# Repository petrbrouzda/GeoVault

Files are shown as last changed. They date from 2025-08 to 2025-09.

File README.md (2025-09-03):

# GeoVault - GPS trezor

Kouzelná krabička, která se sama otevře až na správném místě. A informace, jak najít správné místo, nedává moc konkrétně. Uváděné kilometry k cíli udává po skocích, tj. nestačí si zajít na dvě různá místa a zbytek vyřešit triangulací. 

Kilometry ukazuje po následujících blocích:
```
int kilometers[] = { 2, 3, 5, 10, 18, 30, 55, 72, 82, 90, 110, 150, 200, -1 };
```

Pro vzdálenost menší než 2 km ukazuje metry, opět po skocích:
```
int meters[] = { 1, 10, 20, 50, 100, 200, 300, 500, 750, 1000, 1250, 1500, 1700, 2000, -1 };
```

Box má zhruba 12x12x12 cm, a zvenčí nemá žádné šrouby ani jiné spojovací prvky. Kouká jen USB-C pro nabíjení, vypínač a displej. 

Na správném místě víko samo vyskočí ven.

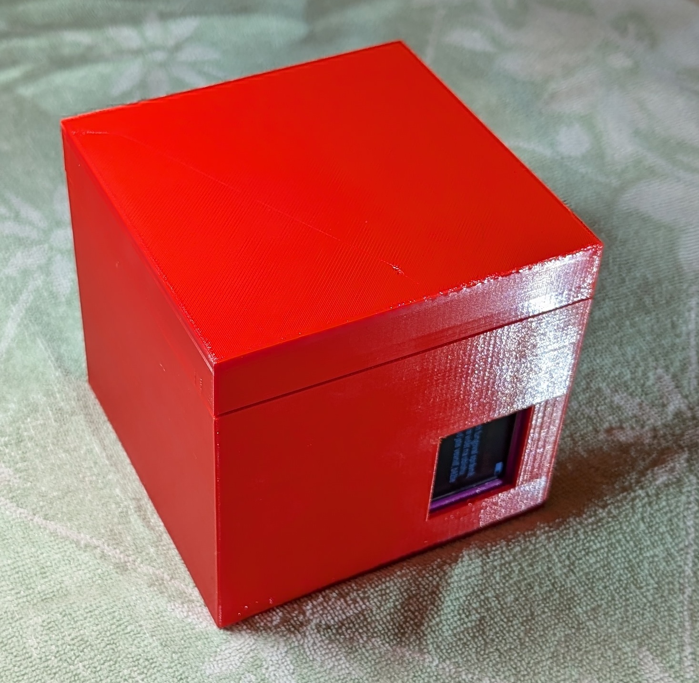
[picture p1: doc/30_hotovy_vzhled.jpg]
Takhle to vypadá z venku
 

Uvnitř je kromě elektroniky úložný prostor cca 58x110x105 mm, do kterého lze umístit cílovou odměnu.

(Na tomhle obrázku chybí na kolících pružinky, které tlačí víko ven - důležitá součástka.)

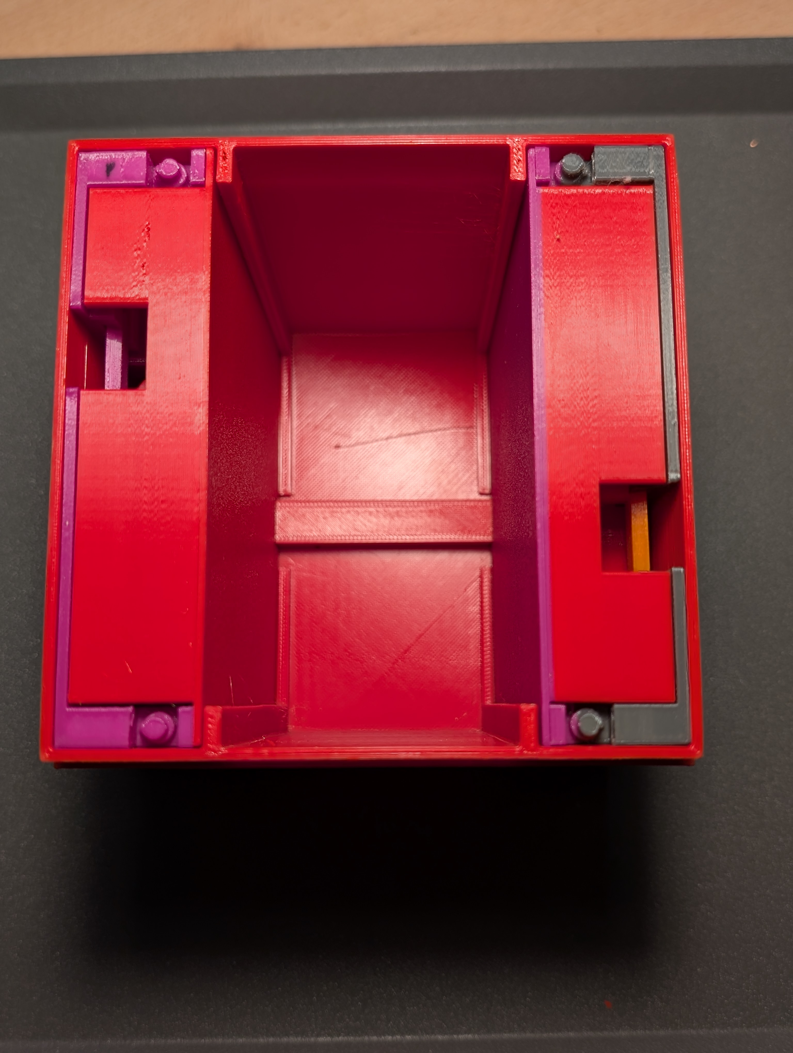
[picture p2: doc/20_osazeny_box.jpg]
Nákladový prostor
 

Co se ukazuje na displeji?

|  |  | 
| --- | --- |
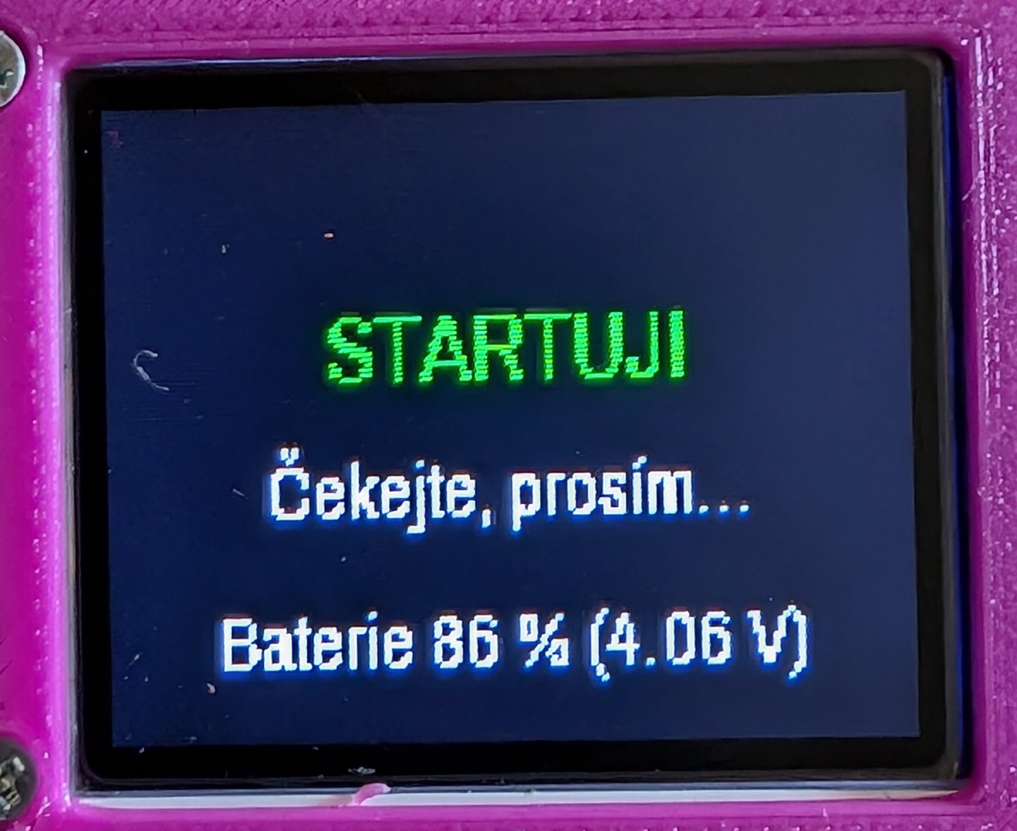
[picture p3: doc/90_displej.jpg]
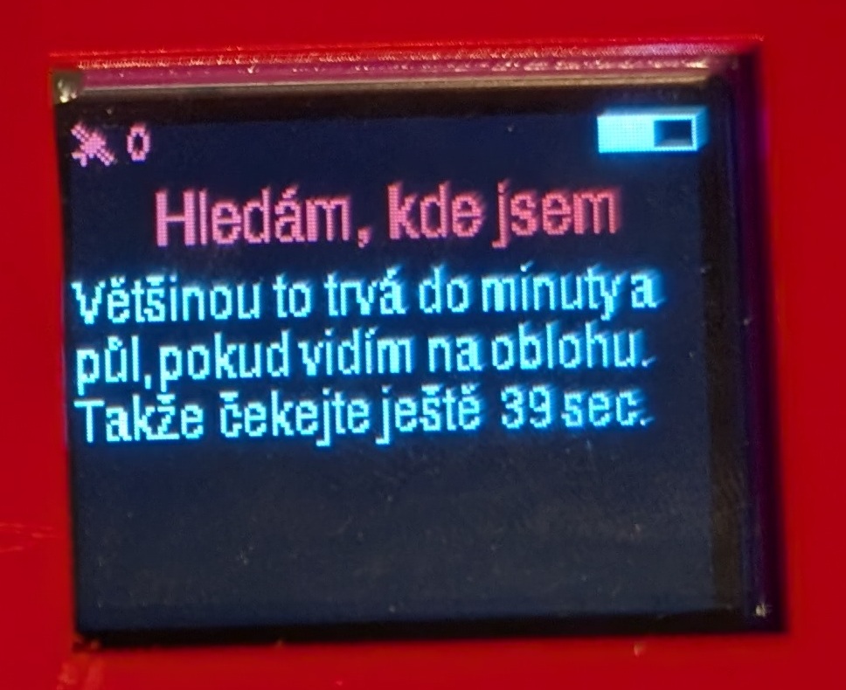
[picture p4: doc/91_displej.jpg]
|   |  |
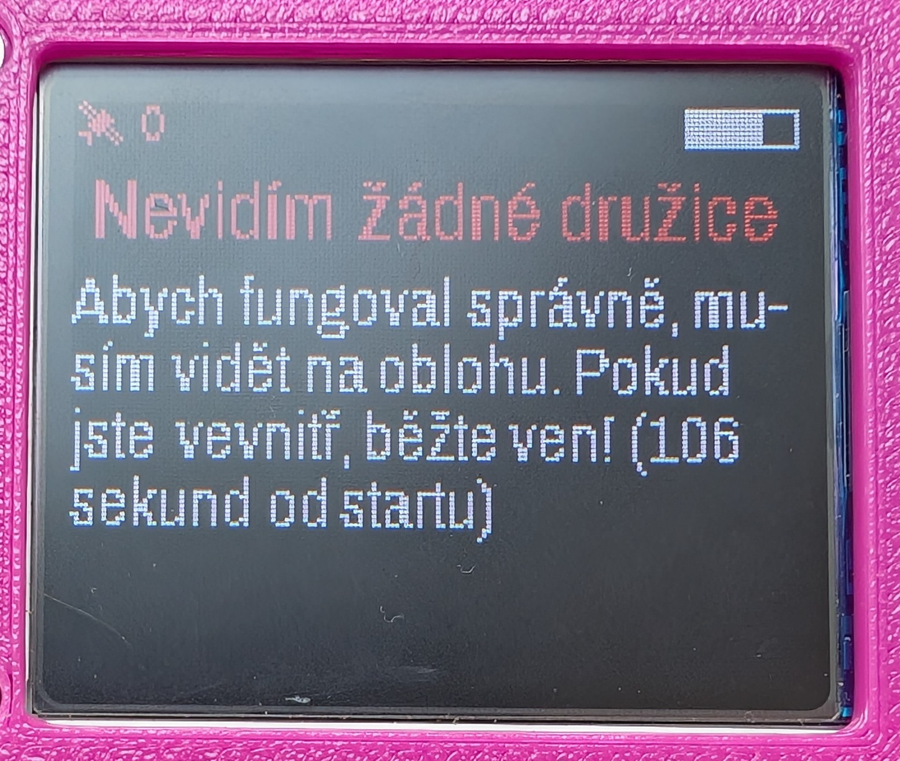
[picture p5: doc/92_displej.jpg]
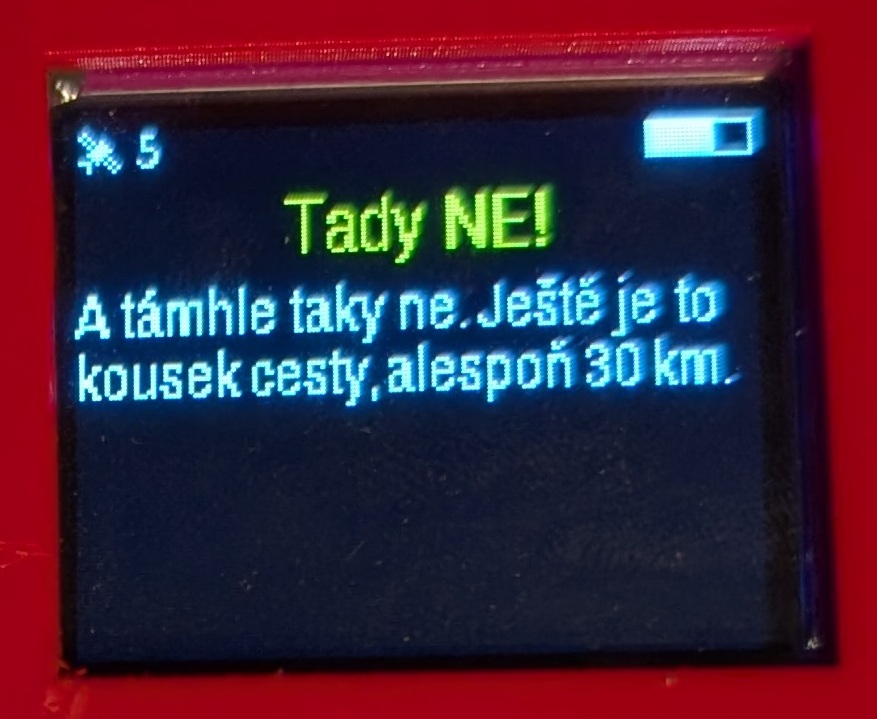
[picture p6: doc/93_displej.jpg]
|   |  |
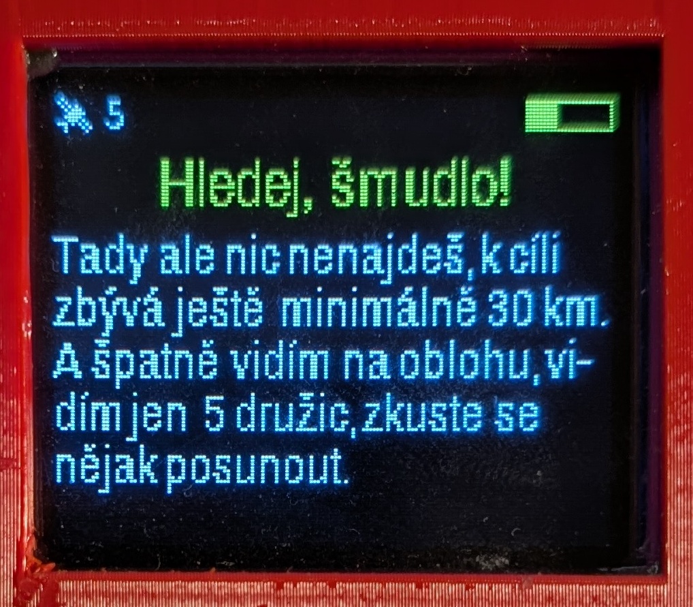
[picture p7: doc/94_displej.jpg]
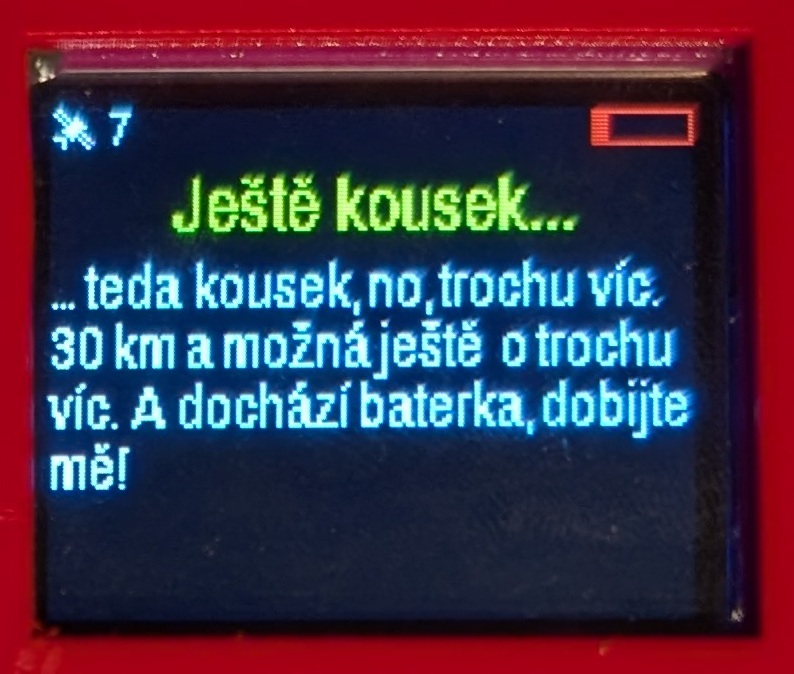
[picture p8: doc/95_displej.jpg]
|   |  |
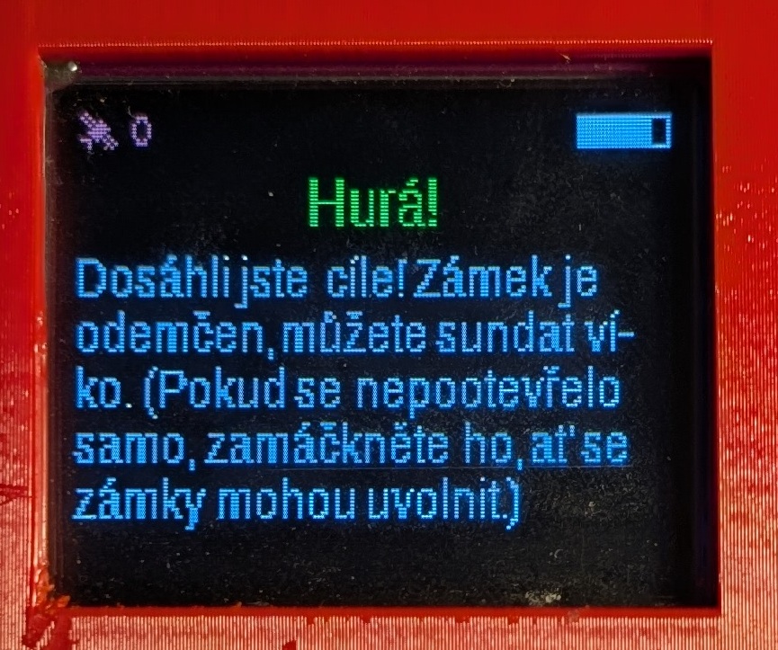
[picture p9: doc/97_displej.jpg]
|   |  |

## Použitá technika

Displej 1.8" 128*160 SPI ST7735S
https://s.click.aliexpress.com/e/_oFWSbIL

GPS modul QUESCAN QU728F NEO-7N 
https://s.click.aliexpress.com/e/_onFHu2X

Kontrolér ESP32 supermini
https://s.click.aliexpress.com/e/_omWAY7h

Modul pro ochranu a dobíjení lipol baterky
https://www.laskakit.cz/nabijecka-li-ion-clanku-tp4056-s-ochranou-usb-c/

Step-up na 5 V
https://www.laskakit.cz/laskakit-bat-boost-menic-5v-0-6a-dio6605b/

Dvě mikroserva 

USB-C konektor zašroubovatelný do stěny krabice
https://s.click.aliexpress.com/e/_oBgHaAr

Malý vypínač 
https://s.click.aliexpress.com/e/_oCtPgSJ

# Sestavení

Schema je [adresáři doc](/doc/schema.svg)

Na každé straně krabičky je jedna deska - na jedné straně napájení (akumulátor, nabíjecí obvod, step-up, vypínač a USB-C konektor) plus servo zámku, na druhé straně procesorová část (mikrokontrolér, GPS, displej) plus servo druhého zámku.

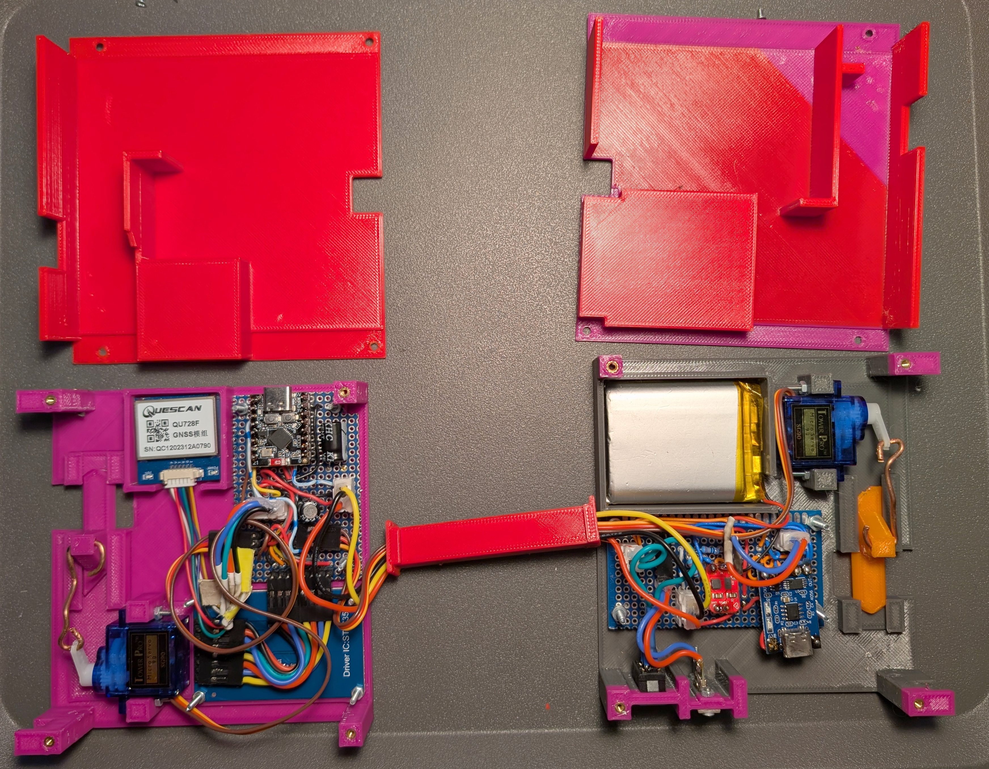
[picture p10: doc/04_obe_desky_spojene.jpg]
Kompletní elektronika
 

Zámek je odvozen od tohoto modelu: https://www.printables.com/model/680586-servo-operated-lock-remix

U serva je potřeba zkontrolovat a případně zkrátit délku páky, aby se otočila pod víkem a nenarážela. 

# Aplikace

Aplikace vystavuje WiFi a na něm webové rozhraní, kde vypisuje stav zařízení, umožňuje otevřít/zavřít zámek a nastavit cílové souřadnice.

* Wifi AP: GeoVault
* heslo: SuperTajneHeslo2

Webový server pak běží na http://192.168.10.1/ , ale WiFi by si mělo samo otevřít prohlížeč po připojení - jako captive portál ("Přihlašte se do sítě WiFi").
Konfigurace wifi a IP adres je v souboru [EasyWebServer_config.h](/GeoVault/EasyWebServer_config.h).

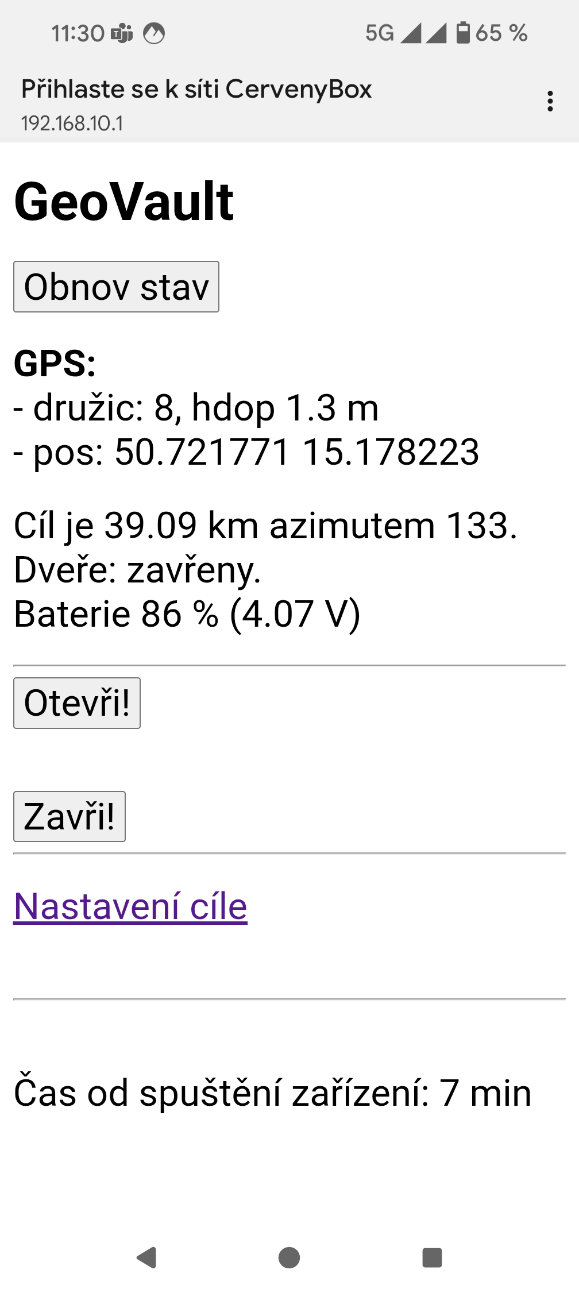
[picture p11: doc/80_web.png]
Webové rozhraní
 

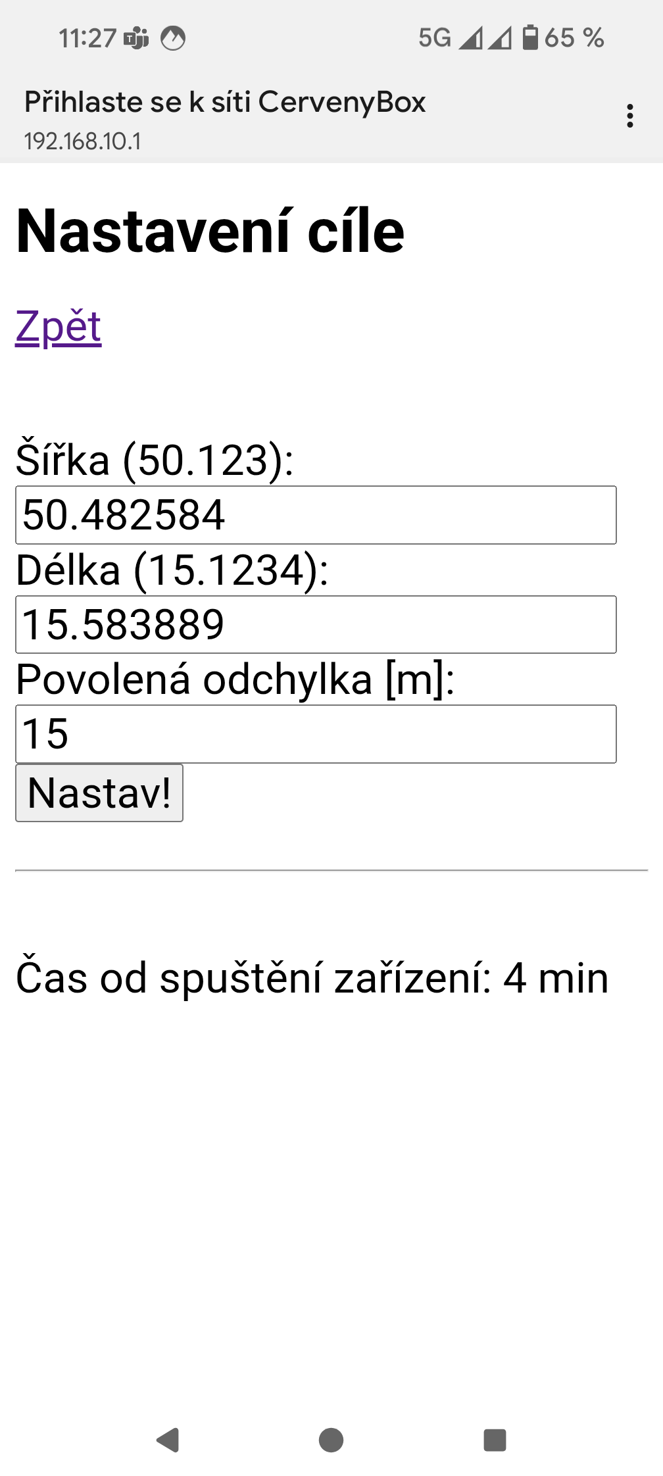
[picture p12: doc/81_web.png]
Nastavení cíle
 

Na speciální adrese http://192.168.10.1/servo lze manuálně nastavit pokyny pro posun serv - aby se dalo nastavit, jaké hodnoty jsou správné pro plné otevření a zavření. Konbfiguraci hodnot je pak potřeba zadat do souboru [pinout.h](/GeoVault/pinout.h) položek

```
#define SERVO1_OTEVRENO 20
#define SERVO1_ZAVRENO 130
#define SERVO1_SMER_OTEVIRANI -1

#define SERVO2_OTEVRENO 20
#define SERVO2_ZAVRENO 130
#define SERVO2_SMER_OTEVIRANI -1
```

## Sestavení aplikace

Verze desky ESP32 v Arduino IDE **musí** být 2.0.x (nyní 2.0.17). Na 3.0.x to fungovat nebude.

Konfigurace desky:
* deska: ESP32C3 Dev module
* flash mode: DIO (jinak tahle deska neběží!)
* CDC On Boot: enabled
* CPU speed: 80 MHz
* flash speed: 40 MHz
* partition scheme: default 4 MB with SPIFFS (1.2 MB APP/1.5 MB SPIFFS)

Knihovny:
* Web server: https://github.com/ESP32Async/ESPAsyncWebServer 3.7.7 a  https://github.com/ESP32Async/AsyncTCP 3.4.0
* ESP32 analog read: https://github.com/madhephaestus/ESP32AnalogRead 0.3.0
* Tasker: https://github.com/joysfera/arduino-tasker 2.0.3
* Displej: Adafruit GFX Library https://github.com/adafruit/Adafruit-GFX-Library 1.12.0 + Adafruit BusIO https://github.com/adafruit/Adafruit_BusIO 1.17.0 + Adafruit ST7735 and ST7789 Library https://github.com/adafruit/Adafruit-ST7735-Library 1.11.0
* GPS: TinyGPSPlus https://github.com/mikalhart/TinyGPSPlus 1.0.3
* Servo: ESP32Servo https://madhephaestus.github.io/ESP32Servo/files.html 3.0.7

Detailní výpis z kompilace:
```
FQBN: esp32:esp32:esp32c3:CDCOnBoot=cdc,CPUFreq=80,FlashFreq=40,FlashMode=dio

Using library Async TCP at version 3.4.0 in folder: E:\dev.moje\arduino\libraries\Async_TCP 
Using library ESP Async WebServer at version 3.7.7 in folder: E:\dev.moje\arduino\libraries\ESP_Async_WebServer 
Using library Tasker at version 2.0.3 in folder: E:\dev.moje\arduino\libraries\Tasker 
Using library Adafruit GFX Library at version 1.12.0 in folder: E:\dev.moje\arduino\libraries\Adafruit_GFX_Library 
Using library Adafruit BusIO at version 1.17.0 in folder: E:\dev.moje\arduino\libraries\Adafruit_BusIO 
Using library Adafruit ST7735 and ST7789 Library at version 1.11.0 in folder: E:\dev.moje\arduino\libraries\Adafruit_ST7735_and_ST7789_Library 
Using library TinyGPSPlus at version 1.0.3 in folder: E:\dev.moje\arduino\libraries\TinyGPSPlus 
Using library ESP32Servo at version 3.0.7 in folder: E:\dev.moje\arduino\libraries\ESP32Servo 
Using library ESP32AnalogRead at version 0.3.0 in folder: E:\dev.moje\arduino\libraries\ESP32AnalogRead 
Using library DNSServer at version 2.0.0 in folder: C:\Users\brouzda\AppData\Local\Arduino15\packages\esp32\hardware\esp32\2.0.17\libraries\DNSServer 
Using library FS at version 2.0.0 in folder: C:\Users\brouzda\AppData\Local\Arduino15\packages\esp32\hardware\esp32\2.0.17\libraries\FS 
Using library WiFi at version 2.0.0 in folder: C:\Users\brouzda\AppData\Local\Arduino15\packages\esp32\hardware\esp32\2.0.17\libraries\WiFi 
Using library Wire at version 2.0.0 in folder: C:\Users\brouzda\AppData\Local\Arduino15\packages\esp32\hardware\esp32\2.0.17\libraries\Wire 
Using library SPI at version 2.0.0 in folder: C:\Users\brouzda\AppData\Local\Arduino15\packages\esp32\hardware\esp32\2.0.17\libraries\SPI 
Using library SPIFFS at version 2.0.0 in folder: C:\Users\brouzda\AppData\Local\Arduino15\packages\esp32\hardware\esp32\2.0.17\libraries\SPIFFS 

```

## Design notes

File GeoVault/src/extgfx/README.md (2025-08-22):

Graphics objects for Adafruit_GFX and Arduino_GFX displays.

Homepage: https://github.com/petrbrouzda/ExtGfx

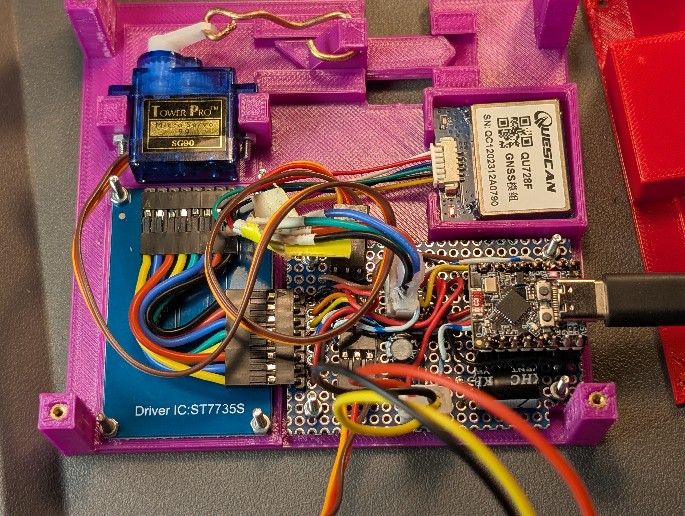
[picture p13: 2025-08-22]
doc/03 deska procesoru GPS a displeje.jpg

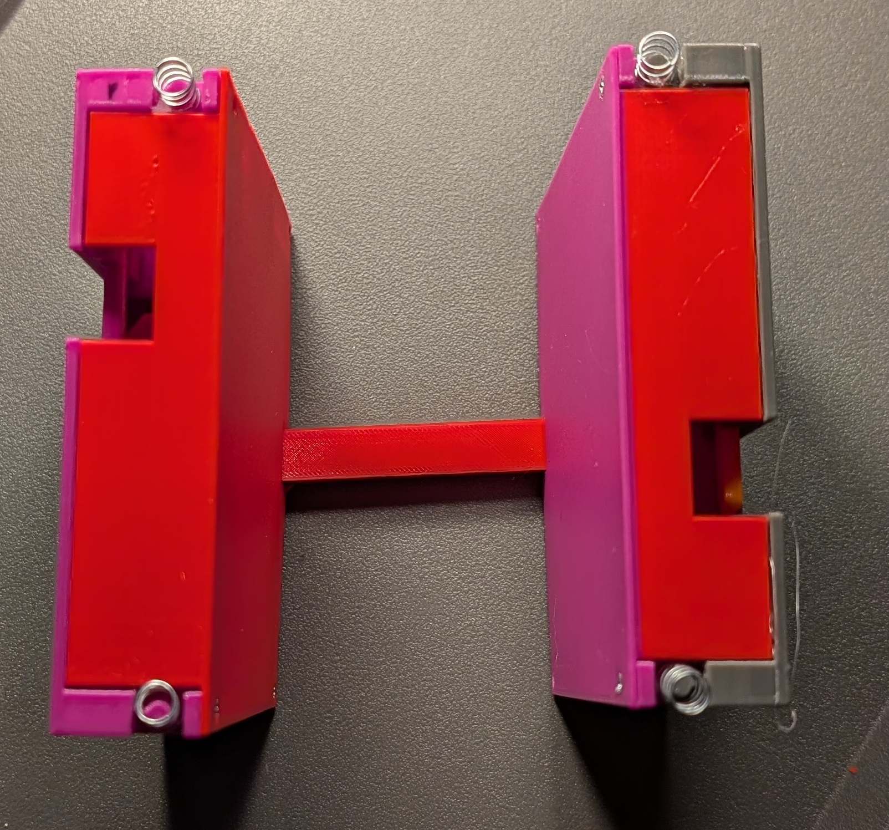
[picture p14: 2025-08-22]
doc/08 dve krabicky pohled shora.jpg

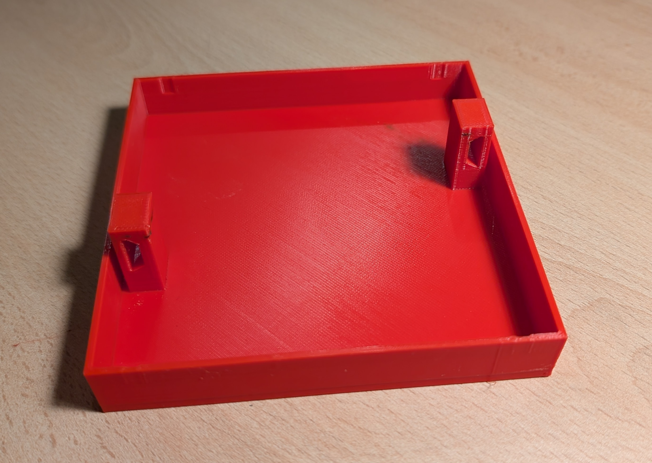
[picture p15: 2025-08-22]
doc/23 viko.jpg

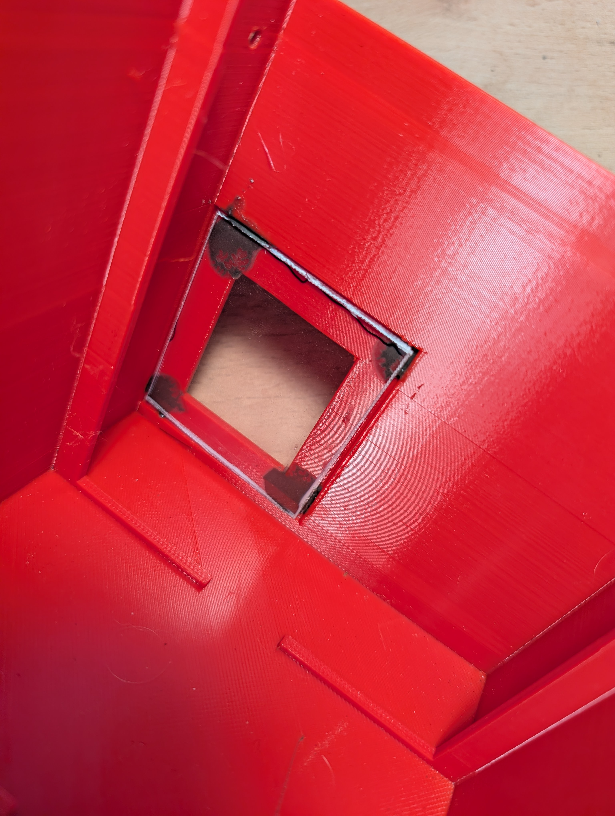
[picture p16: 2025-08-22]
doc/21 kryci sklo displeje nalepene zevnitr.jpg

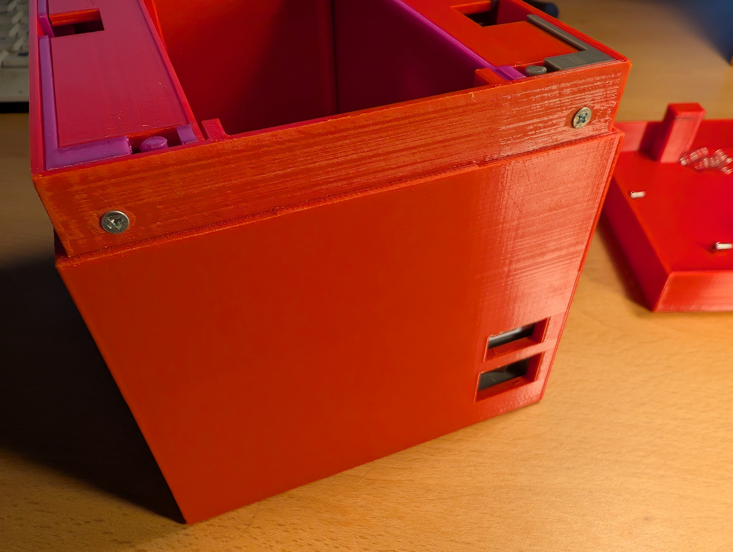
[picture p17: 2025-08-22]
doc/21 jedine srouby jsou zboku kryte vikem.jpg

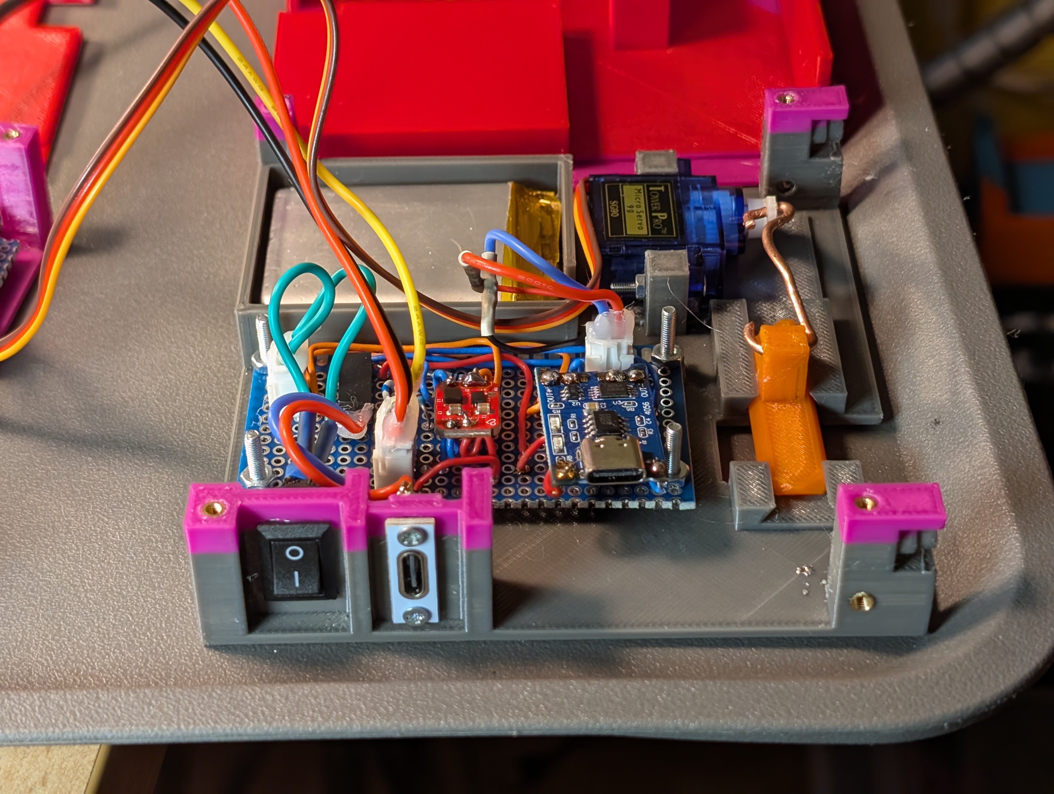
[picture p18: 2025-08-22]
doc/01 deska napajeni.jpg

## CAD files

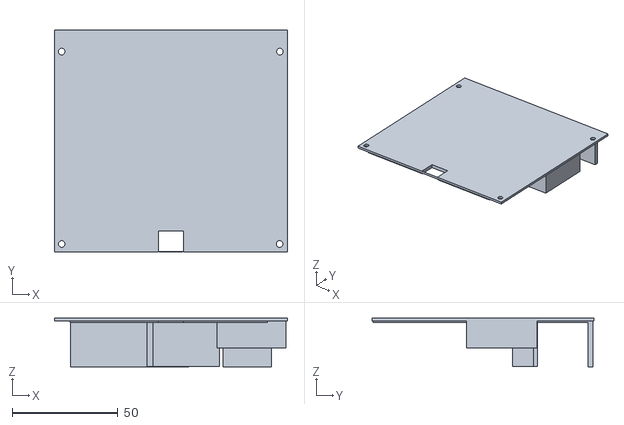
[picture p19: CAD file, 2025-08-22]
stl/GPS trezor g3 - zavírací desky B.stl
110.0 x 104.8 x 23.0

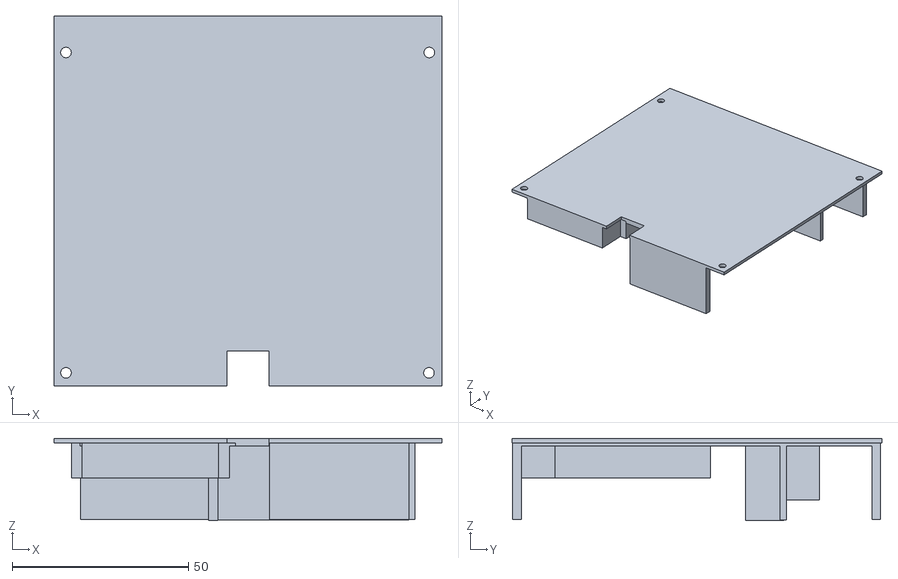
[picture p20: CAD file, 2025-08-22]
stl/GPS trezor g3 - zavírací desky A.stl
110.0 x 104.8 x 23.3

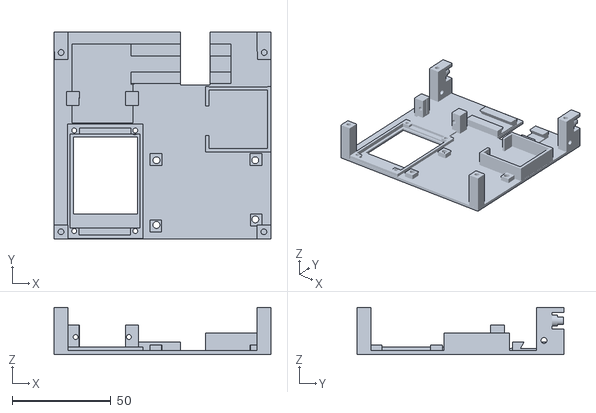
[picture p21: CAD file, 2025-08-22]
stl/GPS trezor g3 - vnitřní blok B - displej a procesor.stl
110.0 x 105.0 x 24.0

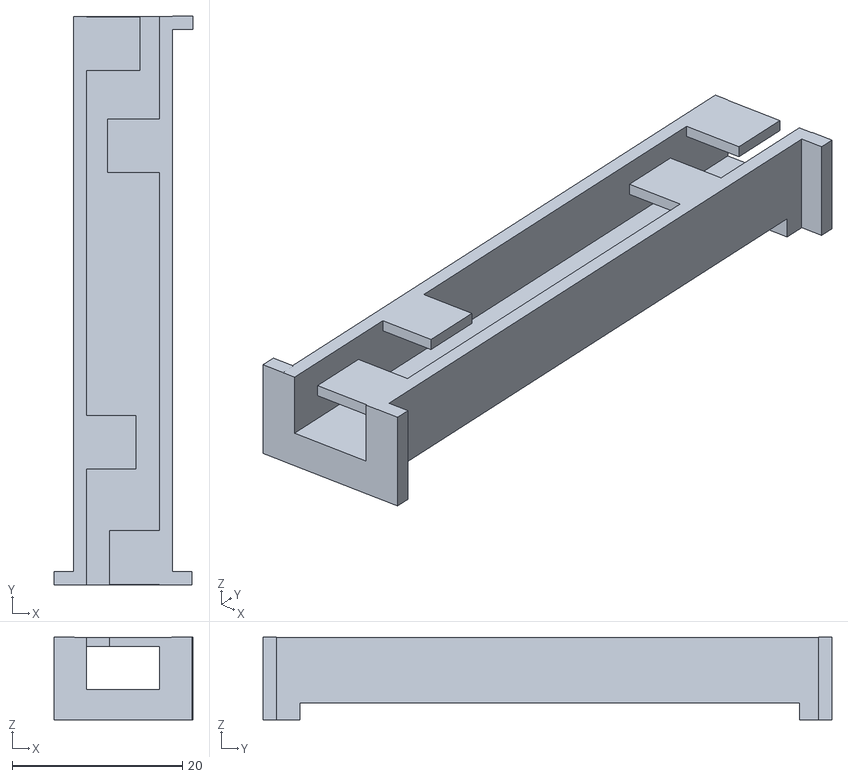
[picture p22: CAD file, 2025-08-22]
stl/gps trezor g3 - kabelová průchodka.stl
16.3 x 66.8 x 9.72

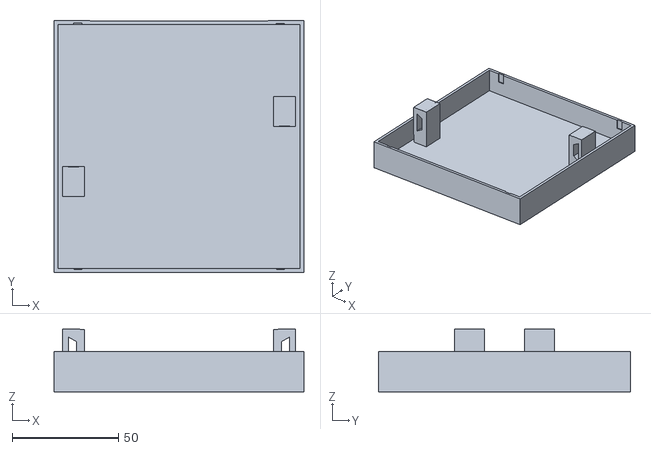
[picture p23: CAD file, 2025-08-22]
stl/GPS trezor g3 - víko.stl
117.9 x 118.7 x 29.5

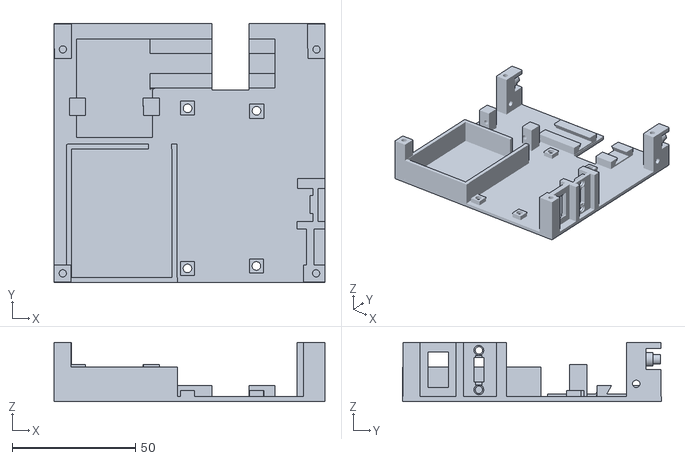
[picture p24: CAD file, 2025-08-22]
stl/GPS trezor g3 - vnitřní blok A - baterky.stl
110.0 x 105.0 x 24.0

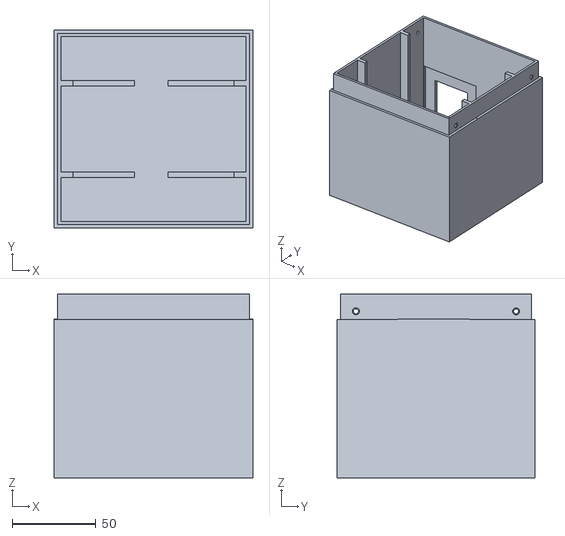
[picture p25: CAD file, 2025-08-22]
stl/GPS trezor g3 - hlavní tělo.stl
118.5 x 118.1 x 109.4

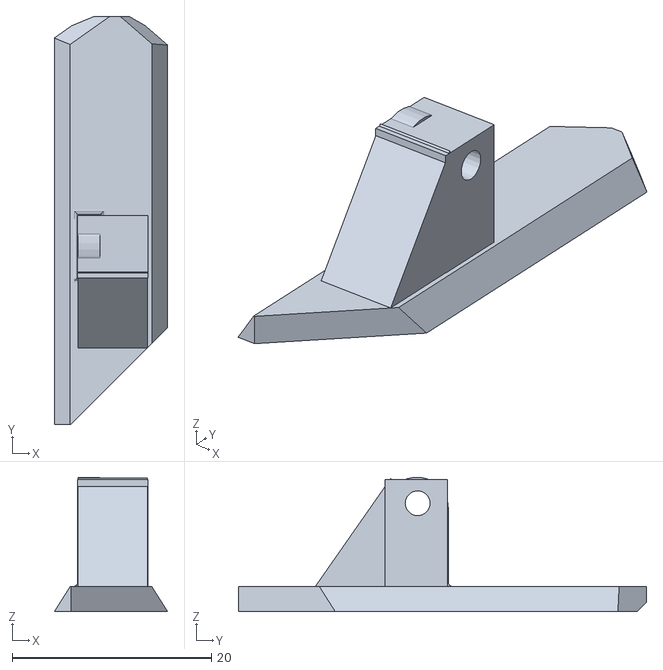
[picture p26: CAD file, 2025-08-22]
stl/GPS trezor g3 - zámek.stl
11.4 x 41.0 x 13.5

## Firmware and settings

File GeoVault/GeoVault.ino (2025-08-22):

// FQBN: esp32:esp32:esp32c3:CDCOnBoot=cdc,CPUFreq=80,FlashFreq=40,FlashMode=dio

// zapojeni
#include "pinout.h"


/* AsyncLogger se pouziva pro logovani udalosti v asynchronnich aktivitach (webserver...).
Uklada zaznamy do pole v pameti a ty se pak vypisou v loop() pomoci volani dumpTo(); */
#include "src/logging/AsyncLogger.h"
AsyncLogger asyncLogger;

#include "src/logging/SerialLogger.h"
SerialLogger serialLogger( &Serial );


/** Sdileny stav aplikace - objekt drzici napr. chybu inicializace MP3, aby se dala vypsat  */
#include "AppState.h"
AppState appState;



/*
WebServer - pres izolacni vrstvu

Pouzivaji se tyto dve knihovny:
- https://github.com/ESP32Async/ESPAsyncWebServer
- https://github.com/ESP32Async/AsyncTCP 
*/
#include "EasyWebServer.h"
EasyWebServer webserver( &asyncLogger );


/*
Konfigurace.
Je nutny alespon kousek filesystemu SPIFFS.
*/
#include "src/toolkit/BasicConfig.h"
#include "src/toolkit/ConfigProviderSpiffs.h"
BasicConfig config;
// může dostat serialLogger, protože poběží synchronně v loopu
ConfigProviderSpiffs configProvider( &serialLogger, &config, &appState);
bool saveConfigChange=false;


/*
Periodicke ulohy
https://github.com/joysfera/arduino-tasker
*/
#define TASKER_MAX_TASKS 10
#include <Tasker.h>
Tasker tasker;


/*
Displej 1.8" 128x160 
*/
#include <Adafruit_GFX.h>    // Core graphics library
#include <Adafruit_ST7735.h> // Hardware-specific library for ST7735
#include "Adafruit_ST77xx.h"
#include <SPI.h>
Adafruit_ST7735 * tft;

// https://github.com/petrbrouzda/ExtGfx
#include "src/extgfx/TextPainter.h"
#include "src/extgfx/HorizontalBar.h"
#include "src/extgfx/BasicColors.h"

// konverze viz https://github.com/petrbrouzda/fontconvert8-iso8859-2
#include "fonts/PragatiNarrow-Regular16pt8b.h"
#include "fonts/PragatiNarrow-Regular20pt8b.h"
#include "fonts/PragatiNarrow-Regular12pt8b.h"

TextPainter * painter;
TpFontConfig malePismo;
TpFontConfig vetsiPismo;
TpFontConfig mikroPismo;



/** 
GPS
http://arduiniana.org/libraries/tinygpsplus/
https://github.com/mikalhart/TinyGPSPlus?tab=readme-ov-file 

GPS pripojena na 3v3 vystup shodi cely cip
ale GPS ma povoleno 3.3-5 V, takze ji lze dat primo na baterku nebo na step-up
*/
#include <TinyGPS++.h>
TinyGPSPlus gps;

HardwareSerial hwSerial_1(1);



// serva 
// https://github.com/madhephaestus/ESP32Servo
// verze 3.0.8 je rozbita, downgrade na 3.0.7!  https://github.com/madhephaestus/ESP32Servo/issues/77
#include <ESP32Servo.h>

Servo servo1;
Servo servo2;


/*
Pro mereni kapacity baterky - kalibrace ADC mereni.
https://github.com/madhephaestus/ESP32AnalogRead 
*/
#include <ESP32AnalogRead.h>
ESP32AnalogRead adc;

#include "src/toolkit/map_double.h"
#include "src/toolkit/mnozne_cislo.h"


//---------- setup

void setup() {
  Serial.begin(115200);

  // nejprve nahodit displej a uvodni obrazovku, pak teprve delat dalsi akce
  
  // ----- displej -----

  SPI.end(); // release standard SPI pins
  SPI.begin(TFT_SCLK, SPI_MISO_UNUSED, TFT_MOSI, TFT_CS); // map and init SPI pins
  // For 1.44" and 1.8" TFT with ST7735 use:
  tft = new Adafruit_ST7735(TFT_CS, TFT_DC, TFT_RST);
  pinMode( TFT_BACKLIGHT, OUTPUT );
  digitalWrite( TFT_BACKLIGHT, HIGH );
  // Use this initializer if using a 1.8" TFT screen:
  tft->initR(INITR_BLACKTAB);      // Init ST7735S chip, black tab
  // SPI speed defaults to SPI_DEFAULT_FREQ defined in the library, you can override it here
  // Note that speed allowable depends on chip and quality of wiring, if you go too fast, you
  // may end up with a black screen some times, or all the time.
  tft->setSPISpeed(40000000);
  tft->setRotation(1);

  // ----- extgfx -----
  // https://github.com/petrbrouzda/ExtGfx

  painter = new TextPainter( tft );
  
  // písmo pro běžné texty
  painter->createFontConfig( &malePismo, &PragatiNarrow_Regular16pt8b );
  malePismo.lineHeight = malePismo.lineHeight - 1;

  // nadpisy
  painter->createFontConfig( &vetsiPismo, &PragatiNarrow_Regular20pt8b );

  // horní lišta - počet družic
  painter->createFontConfig( &mikroPismo, &PragatiNarrow_Regular12pt8b );
  mikroPismo.firstLineHeightOffset -= 2;

  // vykreslime startup info
  uvodniObrazovka();

  // ---- ostatni inicializace --- 

  delay(2500); // aby urcite fungoval seriovy port
  Serial.println( "Startuju!" );

  // pri prvnim startu muze trvat 30 sekund!
  configProvider.openFsAndLoadConfig();

  webserver.startApAndWebserver();

  //  ---- GPS ----- 
  
  //  HW Serial port na daných pinech RX a TX
  // prvni parametr je RX, druhy TX - z pohledu mikrokontroleru
  hwSerial_1.begin(9600, SERIAL_8N1, GPS_TX_PIN, GPS_RX_PIN );
  hwSerial_1.onReceive(serial_callback);

  tasker.setInterval( displayInfo, 10000 );

  // --- servo ----

  ESP32PWM::allocateTimer(0);
  servo1.setPeriodHertz(50);// Standard 50hz servo  
  servo1.attach(SERVO1);
  servo2.setPeriodHertz(50);// Standard 50hz servo  
  servo2.attach(SERVO2);

  servo1.write(SERVO1_ZAVRENO);
  servo2.write(SERVO2_ZAVRENO);


  // --- konfigurace

  char *p = (char*)config.getString( "target_lat", "50.0" );
  appState.targetLat = atof( p );
  p = (char*)config.getString( "target_lon", "15.0" );
  appState.targetLon = atof( p );
  appState.accuracy = config.getLong( "target_accuracy", 50 );


  // baterka

  adc.attach( ACCU_V );
  zmerAccu();
  delay(100);
  zmerAccu();
  uvodniObrazovka();

  // --- spusteni aplikace
  tasker.setTimeout( aktualizujStav, 5000 );  

  generujTextKey();
  
}


#define MAX_TEXTS 5

/** jednou za minutu zmeni texty, ktere se pouzivaji */
void generujTextKey() {
  randomSeed(analogRead(ACCU_V));
  appState.textKey = random(MAX_TEXTS);
  tasker.setTimeout( generujTextKey, 60000 );
}



void serial_callback()
{
  while (hwSerial_1.available() > 0) {
    gps.encode(hwSerial_1.read());
  }
}


void uvodniObrazovka()
{
  tft->fillScreen(ST77XX_BLACK);
  tft->setTextColor(EG_GREEN);
  painter->setFont( &vetsiPismo );
  painter->printLabel( TextPainter::ALIGN_CENTER, 80, 40, (char*)"STARTUJI");
  tft->setTextColor(EG_WHITE);
  painter->setFont( &malePismo );
  painter->printLabel( TextPainter::ALIGN_CENTER, 80, 70, (char*)"Čekejte, prosím...");
  if( appState.accuVoltage > 0.0 ) {
    char text[100];
    sprintf( text, "Baterie %d %% (%.2f V)", appState.accuPercent, appState.accuVoltage );
    painter->printLabel( TextPainter::ALIGN_CENTER, 80, 100, text );
  }
}


int pocetMereni = 0;

// mereni baterky
void zmerAccu() {
  double vin = adc.readVoltage();
  double vreal = vin / (DELIC_R2/(DELIC_R1+DELIC_R2)) / KALIBRACE;
  if( appState.accuVoltage < 0 ) {
    // prvni mereni = rovnou nastavime
    appState.accuVoltage = vreal;
  } 
  // plovouci exponencialni prumer
  if( pocetMereni<10 ) {
    // prvnich nekolik mereni je potreba projet rychle
    appState.accuVoltage = 0.5 * appState.accuVoltage + 0.5 * vreal;
    tasker.setTimeout( zmerAccu, 1000 );
    pocetMereni++;
  } else {
    appState.accuVoltage = 0.8 * appState.accuVoltage + 0.2 * vreal;
    tasker.setTimeout( zmerAccu, 5000 );
  }
  serialLogger.log( "u=%.2f V (%.2f V)\n", appState.accuVoltage, vreal );
  appState.accuPercent = map_double( appState.accuVoltage, 3.2, 4.2, 0.0, 100.0 );
}



/**
 * Zde nastavte routy pro svou aplikaci.
 * Je zavolano z webserveru v dobe volani webserver.startWifiAndWebserver()
 */
void userRoutes( AsyncWebServer * server )
{
  server->on("/", HTTP_GET, onRequestRoot );
  server->on("/target", HTTP_GET, onRequestTarget );
  server->on("/a-target", HTTP_GET, onRequestTargetAction );
  server->on("/a-open", HTTP_GET, onRequestDoorOpen );
  server->on("/a-close", HTTP_GET, onRequestDoorClose );
  server->on("/debug", HTTP_GET, onRequestDebug );
  server->on("/a-debug", HTTP_GET, onRequestDebugAction );
  server->on("/servo", HTTP_GET, onRequestServo );
  server->on("/a-servo", HTTP_GET, onRequestServoAction );
  
}




// ----------- vlastni vykonna cast aplikace (loop)


long lastGpsBytes = 0;
boolean poziceUzByla = false;


void spoctiStav() {

  if( lastGpsBytes==gps.charsProcessed() ) {
    appState.stav = 0;
    return;
  }
  lastGpsBytes=gps.charsProcessed();

  if( !gps.satellites.isValid() || gps.satellites.value()==0 ) {
    appState.stav = 1;
    return;
  }

  if( !gps.location.isValid() ) {
    // nemame pozici
    appState.stav = 2;
    return;
  }

  poziceUzByla = true;

  // mame pozici!
  double distanceM = TinyGPSPlus::distanceBetween(
        gps.location.lat(),
        gps.location.lng(),
        appState.targetLat,
        appState.targetLon);
  appState.vzdalenostMetru = (int)distanceM;

  if( appState.vzdalenostMetru <= appState.accuracy ) {
    appState.stav = 20;
    if( !appState.dvereOtevreny ) {
      appState.servoRequestWaiting = true;
      appState.servoRequest = 1;
    }
  } else {
    if( gps.satellites.value()<6 ) {
      appState.stav = 10;
    } else {
      appState.stav = 11;
    }
  }
}

void vykresliBaterkuADruzice() {

  HbColorProfile c11( 0.0, EG_RED, EG_RED, EG_WHITE, EG_RED, EG_RED, EG_BLACK );
  HbColorProfile c12( 30.0, EG_YELLOW, EG_YELLOW, EG_BLACK, EG_YELLOW, EG_YELLOW, EG_BLACK );
  HbColorProfile c13( 50.0, EG_WHITE, EG_WHITE, EG_BLACK, EG_WHITE, EG_WHITE, EG_BLACK );
  // musi byt zakoncene NULLem; hodnoty musí být seřazené vzestupně
  HbColorProfile *colors1[] = { &c11, &c12, &c13, NULL };

  HorizontalBar hb1( tft, painter );
  hb1.setRange( 0, 100 );
#define ACCU_POS_X 135
  hb1.setPosition( ACCU_POS_X, 1, 160-ACCU_POS_X-1, 8 );
  hb1.setColors( (HbColorProfile**)&colors1 );
  hb1.setFont( &mikroPismo );

  hb1.setValue( (float)appState.accuPercent, (char*)"" );
  hb1.draw();

  if( gps.satellites.isValid() ) {
    char text[256];
    sprintf( text, "\x7f %d", gps.satellites.value() );
    if( gps.satellites.value()<5 ) {
      tft->setTextColor(EG_LIGHT_RED);
    } else {
      tft->setTextColor(EG_WHITE);
    }
    painter->setFont( &mikroPismo );
    painter->startText( 0, 0, 160, 128 );
    painter->printText( text );
  }
  
}

// nadpis
#define POS_X_NADPIS 80
#define POS_Y_NADPIS 15

// text
#define POS_X 0
#define POS_Y 37

void displayNeniGps() {
  tft->setTextColor(EG_LIGHT_RED);
  painter->setFont( &vetsiPismo );
  painter->printLabel( TextPainter::ALIGN_CENTER, POS_X_NADPIS, POS_Y_NADPIS,  (char*)"Není spojení s GPS");

  tft->setTextColor(EG_WHITE);
  painter->setFont( &malePismo );
  painter->startText( POS_X, POS_Y, 160-POS_X-POS_X, 128-POS_Y-1 );
  painter->printText( (char*)"Z GPS přijímače nepřicházejí žádná data. To je podivné.");

  vykresliBaterkuADruzice();
}


#define BEZNY_STARTUP_TIME_MS 90000
#define ROZSIRENY_TEXT_MS 60000


/**
 * Nemam pozici. Ukazuje se ale az 90+ sekund (BEZNY_STARTUP_TIME_MS) po startu.
 */
void displayNeniSignal() {
  tft->setTextColor(EG_LIGHT_RED);
  painter->setFont( &vetsiPismo );
  painter->printLabel( TextPainter::ALIGN_CENTER, POS_X_NADPIS, POS_Y_NADPIS,  (char*)"Nevidím žádné družice");

  tft->setTextColor(EG_WHITE);
  painter->setFont( &malePismo );
  painter->startText( POS_X, POS_Y, 160-POS_X-POS_X, 128-POS_Y-1 );
  char text[256];
  if( poziceUzByla ) {
    sprintf( text, "Abych fungoval správně, musím vidět na oblohu. Pokud jste vevnitř, běžte ven!" );
  } else {
    sprintf( text, "Abych fungoval správně, musím vidět na oblohu. Pokud jste vevnitř, běžte ven! (%d sekund od startu)", millis()/1000L );
  }
  painter->printText( text );

  vykresliBaterkuADruzice();
}



/**
 * Nemam pozici. Ukazuje se prvnich 90 sekund (BEZNY_STARTUP_TIME_MS) po startu.
 */
void displayStartupNeniSignal() {
  tft->setTextColor(EG_LIGHT_RED);
  painter->setFont( &vetsiPismo );
  painter->printLabel( TextPainter::ALIGN_CENTER, POS_X_NADPIS, POS_Y_NADPIS, (char*)"Hledám, kde jsem");

  tft->setTextColor(EG_WHITE);
  painter->setFont( &malePismo );
  painter->startText( POS_X, POS_Y, 160-POS_X-POS_X, 128-POS_Y-1 );
  char text[256];
  int t = ( BEZNY_STARTUP_TIME_MS - millis() ) / 1000L;
  sprintf( text, "Většinou to trvá do minuty a půl, pokud vidím na oblohu. Takže čekejte ještě %d sec.", t );
  if( millis() > ROZSIRENY_TEXT_MS ) {
    strcat( text, " Jsme venku a vidíme na oblohu?" );
  }
  painter->printText( text );
  vykresliBaterkuADruzice();  
}



void displayMaloSignalu() {
  tft->setTextColor(EG_YELLOW);
  painter->setFont( &vetsiPismo );
  painter->printLabel( TextPainter::ALIGN_CENTER, POS_X_NADPIS, POS_Y_NADPIS, (char*)"Čekejte prosím...");

  tft->setTextColor(EG_WHITE);
  painter->setFont( &malePismo );
  painter->startText( POS_X, POS_Y, 160-POS_X-POS_X, 128-POS_Y-1 );
  char text[256];
  sprintf( text, "Hledám, kde jsem. Vidím %d %s, ještě chvilku to bude trvat...", 
    gps.satellites.value(),
    mnozneCislo( gps.satellites.value(), "družici", "družice", "družic" )
  );
  painter->printText( text );

  vykresliBaterkuADruzice();
}


const char *nadpisy[] = {
  "Ještě tam nejsme...",
  "Tady se neotevřu!",
  "Hledej, šmudlo!",
  "Tady NE!",
  "Ještě kousek..."
};

const char * getNadpis() {
  return nadpisy[appState.textKey];
}


char textBuffer[256];

int kilometers[] = { 2, 3, 5, 10, 18, 30, 55, 72, 82, 90, 110, 150, 200, -1 };
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
void loop() {

  // vypiseme asynchronni log, pokud v nem neco je
  asyncLogger.dumpTo( &Serial );

  // aby Tasker spoustel ulohy
  tasker.loop();

  // odbavit DNS pozadavky
  webserver.process();

  // pokud uzivatel zmenil nastaveni, ulozit do souboru a promitnout, kde je potreba
  // nezavesujeme primo na config.isDirty(), protoze bychom mohli trefit nekonzistenci pri nastavovani asynchronne z webserveru
  if( saveConfigChange ) {
    onConfigChanged();
  }

  if( appState.servoRequestWaiting ) {
    provedAkci();
  }

  // na strance 192.168.10.1/servo je mozne rucne nastavit uhel serva - aby se 
  // daly spravne nakonfigurovat hodnoty pro otevirani a zavirani
  if( appState.servoDirectCommand ) {
    servo1.write( appState.servo1Direct);
    servo2.write( appState.servo2Direct);
    appState.servoDirectCommand = false;
  }

}




// -------------- odsud dal je webserver

const char htmlHlavicka[] PROGMEM = R"rawliteral(
  <!DOCTYPE HTML><html>
  <head>
    <title>GeoVault</title>
    <meta name="viewport" content="width=device-width, initial-scale=1">
    <style>
      html {font-family: Arial; display: inline-block; text-align: left;}
      h2 {font-size: 2.0rem;}
      h3 {font-size: 1.65rem; font-weight: 600}
      p {font-size: 1.4rem;}
      input {font-size: 1.4rem;}
      input#text {width: 100%;}
      select {font-size: 1.4rem;}
      form {font-size: 1.4rem;}
      body {max-width: 600px; margin:10px ; padding-bottom: 25px;}
    </style>
  </head>
  <body>
)rawliteral";

const char htmlPaticka[] PROGMEM = R"rawliteral(
  </body>
  </html>
)rawliteral";




const char htmlZacatek[] PROGMEM = R"rawliteral(
  <h1>GeoVault</h1>
  <form method="GET" action="/?">
  <input type="submit" name="obnov" value="Obnov stav" > 
  </form>
)rawliteral";





void vlozInformace( AsyncResponseStream *response )  {
  if( appState.isProblem() ) {
    response->printf( "<p><b>%s:</b> [%s] před %d sec.</p>",
      appState.globalState==ERROR ? "Chyba" : "Varování",
      appState.problemDesc,
      (millis()-appState.problemTime) / 1000L
    );  
  }

  response->print( "<p><b>GPS:</b>" );
  response->print( "<br>" );
  if( gps.satellites.isValid() ) {
    response->printf( "- družic: %d, hdop %.1f m", 
      gps.satellites.value(),
      gps.hdop.isValid() ?  gps.hdop.hdop() : -1.0  );
  } else {
    response->printf( "- družic: ***" );
  }
  response->print( "<br>" );
  if( gps.location.isValid()) {
    response->printf( "- pos: %f %f", 
      gps.location.lat(), 
      gps.location.lng()
    );
  } else {
    response->printf( "- pos: ***" );
  }
  response->print( "</p><p>" );

  if( gps.location.isValid()) {
    double distanceKm = TinyGPSPlus::distanceBetween(
        gps.location.lat(),
        gps.location.lng(),
        appState.targetLat,
        appState.targetLon) 
        / 1000.0;
    double courseTo = TinyGPSPlus::courseTo(
        gps.location.lat(),
        gps.location.lng(),
        appState.targetLat,
        appState.targetLon);
    response->printf( "Cíl je %.2f km azimutem %.0f.",  distanceKm, courseTo );
  }

  response->printf( "<br>Dveře: %s.", appState.dvereOtevreny ? "otevřeny" : "zavřeny" );
  response->printf("<br>Baterie %d %% (%.2f V)</p>", appState.accuPercent, appState.accuVoltage );
}


void vlozUptime( AsyncResponseStream *response ) {
  response->printf( "<br><hr><br><p>Čas od spuštění zařízení: %d min</p>",
    millis()/60000L
  );
}


/** 
 * Je lepe misto Serial.print pouzivat AsyncLogger.
 * Je volano z webserveru asynchronne.
 * Nevolat odsud dlouhotrvajici akce!
 * I logovani by melo byt pres asyncLogger!
 * 
 * Kazda funkce onRequest* musi byt zaregistrovana v userRoutes()
 * 
 */
void onRequestRoot(AsyncWebServerRequest *request){
  asyncLogger.log( "@ req root" );

  AsyncResponseStream *response = request->beginResponseStream(webserver.HTML_UTF8);
  response->print( htmlHlavicka );
  response->print( htmlZacatek );
  vlozInformace( response );
  response->print( "<hr>" );
  response->print( "<form method=\"GET\" action=\"/a-open?\"><input type=\"submit\" name=\"open\" value=\"Otevři!\"></form>" );
  response->print( "<br>&nbsp;<br>" );
  response->print( "<form method=\"GET\" action=\"/a-close?\"><input type=\"submit\" name=\"close\" value=\"Zavři!\"></form>" );
  response->print( "<hr><p><a href=\"/target\">Nastavení cíle</a></p>" );

  vlozUptime( response );
  response->print( htmlPaticka );
  request->send(response);
}


void onRequestTarget(AsyncWebServerRequest *request){
  asyncLogger.log( "@ req target" );

  AsyncResponseStream *response = request->beginResponseStream(webserver.HTML_UTF8);
  response->print( htmlHlavicka );
  response->print( "<h1>Nastavení cíle</h1>" );
  response->print( "<p><a href=\"/\">Zpět</a></p>" );
  response->print( "<form method=\"GET\" action=\"/a-target\">" );
  response->printf( "<br>Šířka (50.123):<br><input type=\"text\" name=\"lat\" value=\"%f\">",  appState.targetLat );
  response->printf( "<br>Délka (15.1234):<br><input type=\"text\" name=\"lon\" value=\"%f\">",  appState.targetLon );
  response->printf( "<br>Povolená odchylka [m]:<br><input type=\"text\" name=\"acc\" value=\"%d\">",  appState.accuracy );
  response->print( "<br><input type=\"submit\" name=\"save\" value=\"Nastav!\"></form>" );

  vlozUptime( response );
  response->print( htmlPaticka );
  request->send(response);
}


void onRequestTargetAction(AsyncWebServerRequest *request){
  asyncLogger.log( "@ req target save" );

  const char * p = webserver.getQueryParamAsString( request, "lat", "50.0" );
  config.setValue( "target_lat", p );
  appState.targetLat = atof( p );

  p = webserver.getQueryParamAsString( request, "lon", "15.0" );
  config.setValue( "target_lon", p );
  appState.targetLon = atof( p );

  long v = webserver.getQueryParamAsLong( request, "acc", 100 );
  config.setValue( "target_accuracy", v );
  appState.accuracy = v;

  saveConfigChange = true;

  request->redirect( "/target" );
}


void onRequestDebug(AsyncWebServerRequest *request){
  asyncLogger.log( "@ req debug" );

  AsyncResponseStream *response = request->beginResponseStream(webserver.HTML_UTF8);
  response->print( htmlHlavicka );
  response->print( "<h1>Debug</h1>" );
  response->print( "<p><a href=\"/\">Zpět</a></p>" );
  response->print( "<form method=\"GET\" action=\"/a-debug\">" );
  response->printf( "<br>Vzdálenost [m]:<br><input type=\"text\" name=\"vzd\" value=\"%d\">",  appState.vzdalenostMetru );
  response->printf( "<br>Stav 10-11:<br><input type=\"text\" name=\"stav\" value=\"%d\">",  appState.stav );
  response->print( "<br><input type=\"submit\" name=\"save\" value=\"Nastav!\"></form>" );

  vlozUptime( response );
  response->print( htmlPaticka );
  request->send(response);
}

void onRequestDebugAction(AsyncWebServerRequest *request){
  asyncLogger.log( "@ req debug action" );

  long vzd = webserver.getQueryParamAsLong( request, "vzd", 100 );

  appState.debugMode = true;

  appState.vzdalenostMetru = vzd;
  appState.stav = webserver.getQueryParamAsLong( request, "stav", 11 );;

  if( vzd < appState.accuracy ) {
    appState.servoRequestWaiting = true;
    appState.servoRequest = 1;
    appState.stav = 20;
  }

  request->redirect( "/debug" );
}

void onRequestServo(AsyncWebServerRequest *request){
  asyncLogger.log( "@ req servo" );

  AsyncResponseStream *response = request->beginResponseStream(webserver.HTML_UTF8);
  response->print( htmlHlavicka );
  response->print( "<h1>Servo</h1>" );
  response->print( "<p><a href=\"/\">Zpět</a></p>" );
  response->print( "<form method=\"GET\" action=\"/a-servo\">" );
  response->printf( "<br>Servo 1 (0-180):<br><input type=\"text\" name=\"s1\" value=\"%d\">",  appState.servo1Direct );
  response->printf( "<br>Servo 2 (0-180):<br><input type=\"text\" name=\"s2\" value=\"%d\">",  appState.servo2Direct );
  response->print( "<br><input type=\"submit\" name=\"save\" value=\"Nastav!\"></form>" );

  vlozUptime( response );
  response->print( htmlPaticka );
  request->send(response);
}

void onRequestServoAction(AsyncWebServerRequest *request){
  asyncLogger.log( "@ req servo action" );

  appState.servo1Direct = webserver.getQueryParamAsLong( request, "s1", 100 );
  appState.servo2Direct = webserver.getQueryParamAsLong( request, "s2", 100 );
  appState.servoDirectCommand = true;

  request->redirect( "/servo" );
}


void onRequestDoorOpen(AsyncWebServerRequest *request){
  asyncLogger.log( "@ req open" );

  appState.servoRequestWaiting = true;
  appState.servoRequest = 1;

  request->redirect( "/" );
}


void onRequestDoorClose(AsyncWebServerRequest *request){
  asyncLogger.log( "@ req close" );

  appState.servoRequestWaiting = true;
  appState.servoRequest = 2;

  request->redirect( "/" );
}


/**
ESP32 2.0.17
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

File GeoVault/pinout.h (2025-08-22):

#ifndef __PINOUT_H__
#define __PINOUT_H__

// ------------ displej ---------------------

#define TFT_CS   5
#define TFT_RST  3
#define TFT_DC   1
#define TFT_MOSI 6
#define TFT_SCLK 4
#define SPI_MISO_UNUSED -1
// LOW = vypnuto, HIGH = zapnuto
#define TFT_BACKLIGHT 8

// ------------ GPS ----------------------

/** ESP32 TX - GPS RX */
#define GPS_RX_PIN 21
/** ESP32 RX - GPS Tx */
#define GPS_TX_PIN 20
#define GPS_BAUD 9600

// ------------ servo ---------------------

#define SERVO1 7
#define SERVO2 10

#define SERVO1_OTEVRENO 20
#define SERVO1_ZAVRENO 130
#define SERVO1_SMER_OTEVIRANI -1

#define SERVO2_OTEVRENO 20
#define SERVO2_ZAVRENO 130
#define SERVO2_SMER_OTEVIRANI -1


// ------------ akumulator ---------------------

#define ACCU_V 0

// POZOR! Hodnota musi byt float, takze .0 na konci
#define DELIC_R1 68000.0
// POZOR! Hodnota musi byt float, takze .0 na konci
#define DELIC_R2 20000.0
// kalibrace - hodnota namerena / hodnota spravna
#define KALIBRACE (2.90/3.72)

#endif

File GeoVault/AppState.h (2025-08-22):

#ifndef ___APP_STATUS_H_
#define ___APP_STATUS_H_



/*
Sdílený stav celé aplikace.
Používá se, aby asynchronní akce ve webserveru měly přístup ke všemu, co potřebují.
*/

#define STATUS_TEXT_MAX_LEN 255


enum ProblemLevel {
    NONE,
    WARNING,
    ERROR
};

class AppState
{
    public:

        AppState();

        //--- evidence problemu, common funkcionalita

        ProblemLevel globalState;
        char problemDesc[STATUS_TEXT_MAX_LEN + 5];
        long problemTime;

        void setProblem( ProblemLevel appState, const char * text );
        void clearProblem();

        bool isProblem();

        //---- per-app funkcionalita

        /** sirka */
        double targetLat;
        /** delka */
        double targetLon;
        /** max. odchylka od cile pro otevreni */
        long accuracy;


        /**
         * 0 = Nemame spojeni s GPS
         * 1 = Zadne satelity
         * 2 = Nejake satelity, zadny fix
         * 10 = Mame pozici, ale malo druzic
         * 11 = Mame pozici
         * 20 = V cili
         */
        int stav = 0;

        int vzdalenostMetru = -1;

        /** stav dveri */
        bool dvereOtevreny = false;

        /** true = otevri dvere */
        bool servoRequestWaiting = false;
        /** 
         * 0 = nic
         * 1 = otevri
         * 2 = zavri
         */
        int servoRequest = 0;


        bool debugMode = false;

        bool servoDirectCommand = false;
        int servo1Direct = 0;
        int servo2Direct = 0;


        double accuVoltage = -1.0;
        int accuPercent = 0;

        /** ktery text se nyni pouziva */
        int textKey = 0;

};

#endif
